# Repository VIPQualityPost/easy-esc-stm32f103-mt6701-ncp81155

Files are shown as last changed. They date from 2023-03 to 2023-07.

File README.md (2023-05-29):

# easy-esc-stm32f103-mt6701-ncp81155

Small, closed loop simpleFOC driver board, that can be assembled for &lt;$10 with mostly basic components at LCSC. has support for current sensing and mounting WS2812 RGBLED for indicating, as well as USB C for serial communication and programming. SWD + UART via STLINK 14 pin connector.

The targe for this project was to create an all-in-one simpleFOC board with high resolution magnetic encoder, current sensing, simpleFOC BLDC driver board which can be assembled with top-side only components, 2 layers, mostly basic components from LCSC library, and which can be powered entirely from USB 2.0 specification (500mA) for mostly use with haptic texture type applications. Additionally, it has a compact size of 38x38mm.

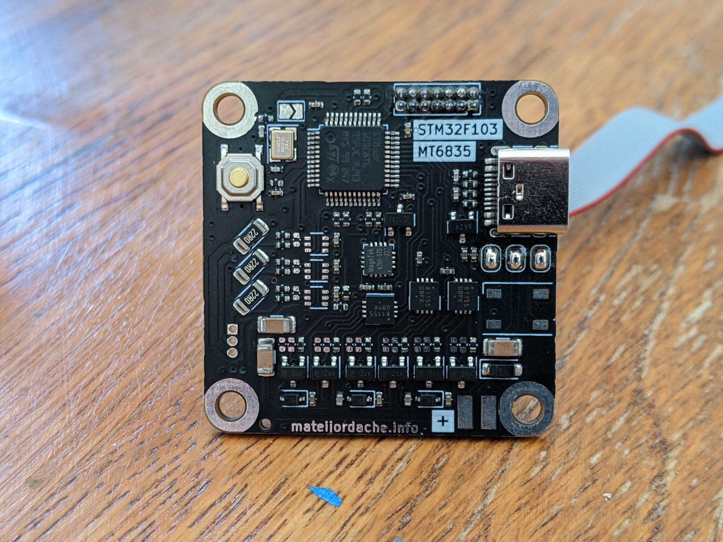
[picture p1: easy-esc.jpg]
3D render of PCB


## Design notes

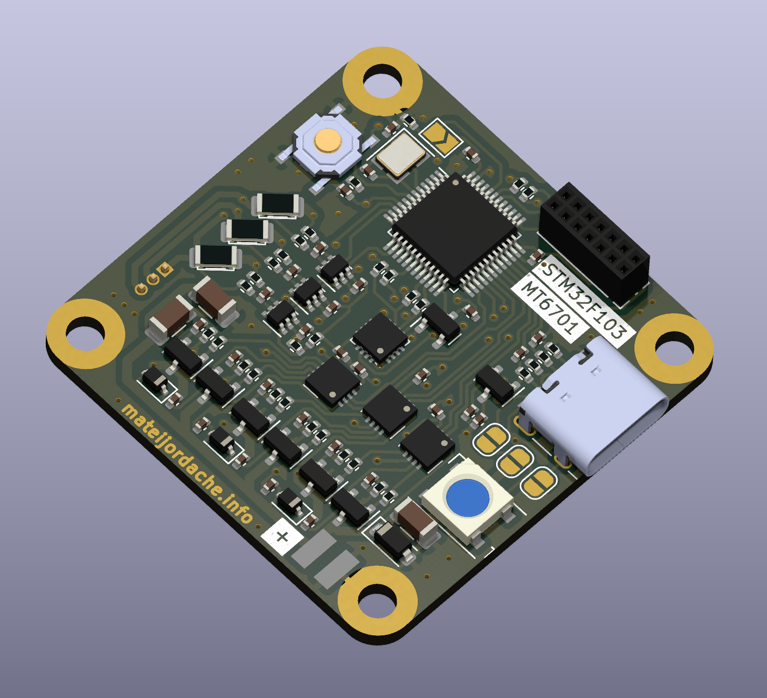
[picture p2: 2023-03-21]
render.png

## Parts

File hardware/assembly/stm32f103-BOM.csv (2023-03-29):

Comment | Designator | Footprint | LCSC
5K | R102,R101 | 0402_R
22R | R106,R107 | 0402_R
1uF | C206,C201,C210,C107,C106 | 0402_C
WS2812 | D101 | SMD_5050
0R | R209,R207,R223,R203,R201,R217,R213,R202,R113,R220,R218,R208,R112,R214,R110,R109 | 0402_R
NCP81155 | U205,U201,U206 | DFN-8_3x3mm | C173765
0.1uF | C101,C212,C218,C211,C109,C111,C110,C108 | 0402_C
1N5819WS | D201,D202,D203 | D_SOD-323 | C191023
22R | R215,R216,R221 | 1206_R
47pF | C105,C104 | 0402_C
10k | R219,R108,R103,R222 | 0402_R
RESET | SW101 | TS-1187A-B-A-B | C318884
LT199 | U204,U203,U202 | SOT-363_SC-70-6 | C2888104
10uF | C214,C215 | 0402_C
AO3400A | Q201,Q205,Q203,Q202,Q101,Q206,Q204 | SOT-23 | C20917
470nF | C222,C205,C223 | 0402_C
5.1k | R105,R104 | 0402_R
20pF | C102,C103 | 0402_C
12MHz | Y101 | Crystal_SMD_3225
HIROSE TYPE C | J101 | HRO_TYPE-C-31-M-12 | C165948
100uF | C221,C220,C213 | 1206_C
STM32F103 | U103 | LQFP-48_7x7mm | C8734
XC6206 | U102 | SOT-23 | C5446
B5819W SL | D204 | D_SOD-123 | C8598
MT6701 | U101 | QFN-16-1EP_3x3mm | C2913974

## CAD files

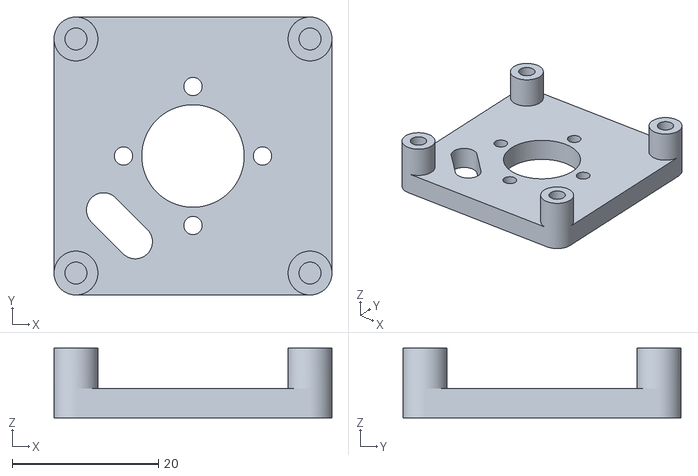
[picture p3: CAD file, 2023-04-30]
mechanical/motormount_b.stl
38.0 x 38.0 x 9.50

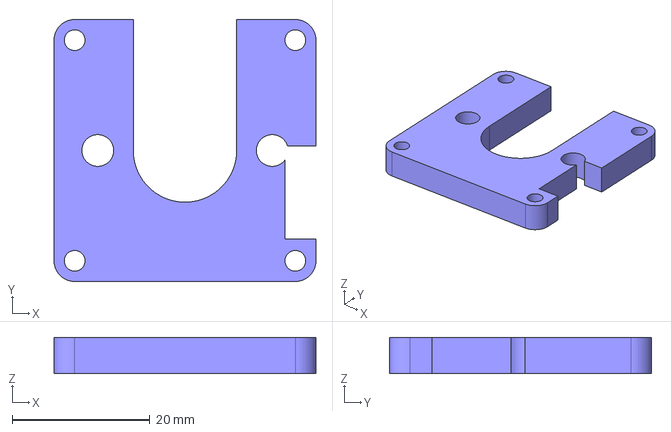
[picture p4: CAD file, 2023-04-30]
mechanical/stm32f103-motormount-back.FCStd
38.0 x 38.0 x 5.25 mm

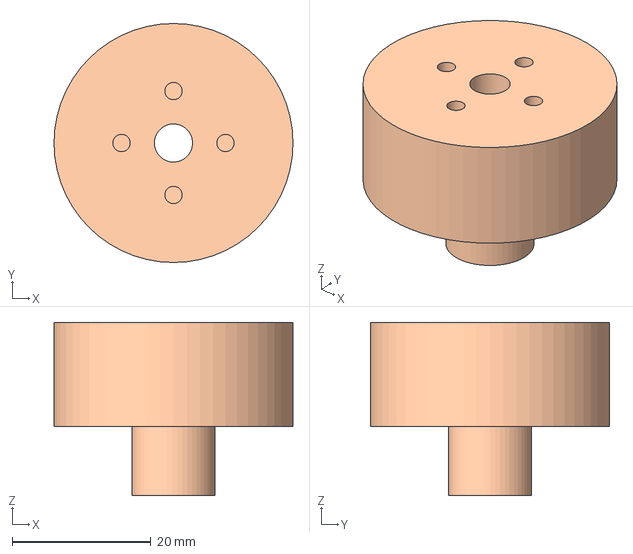
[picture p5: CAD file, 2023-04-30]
mechanical/aliexpress-motor.step
34.5 x 34.5 x 25.0 mm

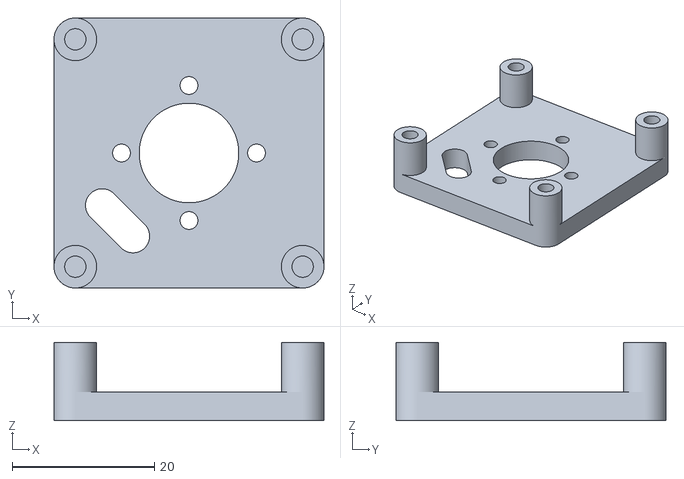
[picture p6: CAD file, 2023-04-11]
mechanical/motormount_test.stl
38.0 x 38.0 x 11.0

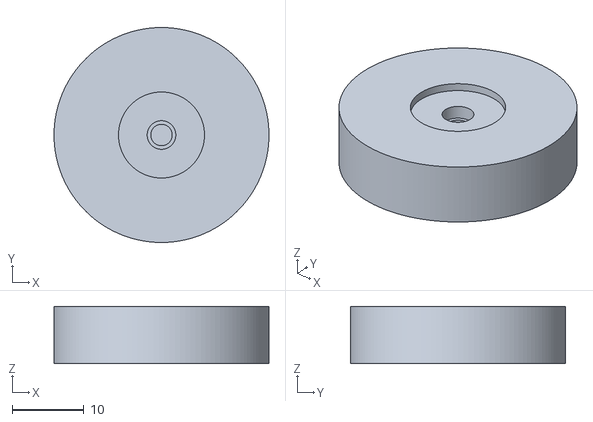
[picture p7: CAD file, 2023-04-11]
mechanical/stm32f103-motormount-back-rotor.stl
30.0 x 30.0 x 8.00

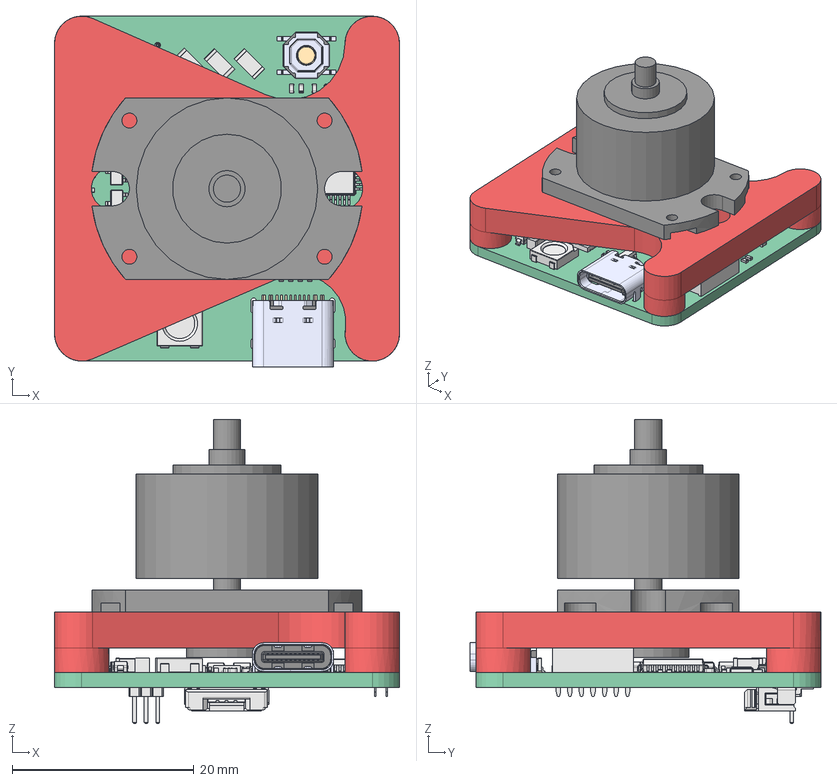
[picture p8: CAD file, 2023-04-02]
mechanical/motormount_front.FCStd
38.0 x 38.6 x 33.5 mm
Pcb_4694
R102_R_0402_1005Metric_309814046252 x 32
C206_C_0402_1005Metric_fbdf68a0e481 x 31
D101_LED_WS2812B_PLCC4_50x50mm_P32mm_7daec3bb67ea
U205_DFN-8-1EP_3x3mm_Pitch0.5mm_7c234c2a8eed x 3
D201_D_SOD_323_6a913e7e0da0 x 3
R215_R_1206_3216Metric_333bfd7ba96b x 3
TS-1187A-B-A-B
TS-1187A-B-A-B001
TS-1187A-B-A-B002
TS-1187A-B-A-B003
TS-1187A-B-A-B004
TS-1187A-B-A-B005
TS-1187A-B-A-B006
U204_SOT_363_SC_70_6_1469dd1663e2 x 3
Q201_SOT_23_4d359ea561da x 8
J102_PinSocket_2x07_P127mm_Vertical_f2266e31e4ba
Y101_Crystal_SMD_3225-4Pin_3.2x2.5mm_af7dcb7e999e
TYPE-C-31-M-12
TYPE-C-31-M-013
TYPE-C-31-M-014
TYPE-C-31-M-015
TYPE-C-31-M-016
TYPE-C-31-M-017
TYPE-C-31-M-018
TYPE-C-31-M-019
TYPE-C-31-M-020
TYPE-C-31-M-021
TYPE-C-31-M-022
TYPE-C-31-M-023
TYPE-C-31-M-024
TYPE-C-31-M-025
TYPE-C-31-M-026
TYPE-C-31-M-027
TYPE-C-31-M-028
TYPE-C-31-M-029
TYPE-C-31-M-030
TYPE-C-31-M-031
TYPE-C-31-M-032
TYPE-C-31-M-033
TYPE-C-31-M-034
TYPE-C-31-M-035
TYPE-C-31-M-036
TYPE-C-31-M-037
TYPE-C-31-M-038
TYPE-C-31-M-039
TYPE-C-31-M-040
TYPE-C-31-M-041
TYPE-C-31-M-042
TYPE-C-31-M-043
TYPE-C-31-M-044
TYPE-C-31-M-045
TYPE-C-31-M-046
TYPE-C-31-M-047
TYPE-C-31-M-048
TYPE-C-31-M-049
TYPE-C-31-M-050
TYPE-C-31-M-051
TYPE-C-31-M-052
TYPE-C-31-M-053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

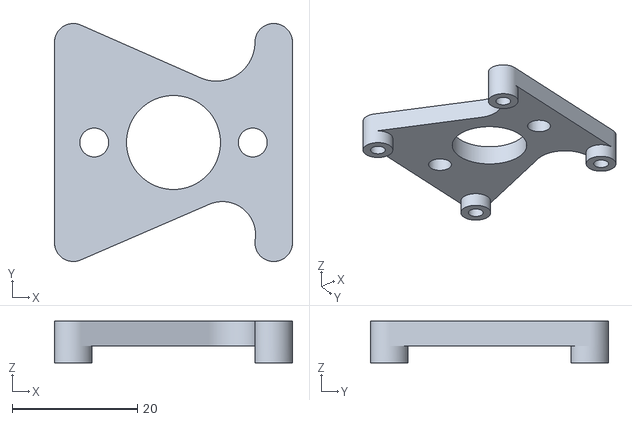
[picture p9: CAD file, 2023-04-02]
mechanical/stm32f103-motormount_top.stl
38.0 x 38.0 x 6.70

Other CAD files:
mechanical/motormount-back-stlinkcutout.stl
mechanical/motormount_back.stl

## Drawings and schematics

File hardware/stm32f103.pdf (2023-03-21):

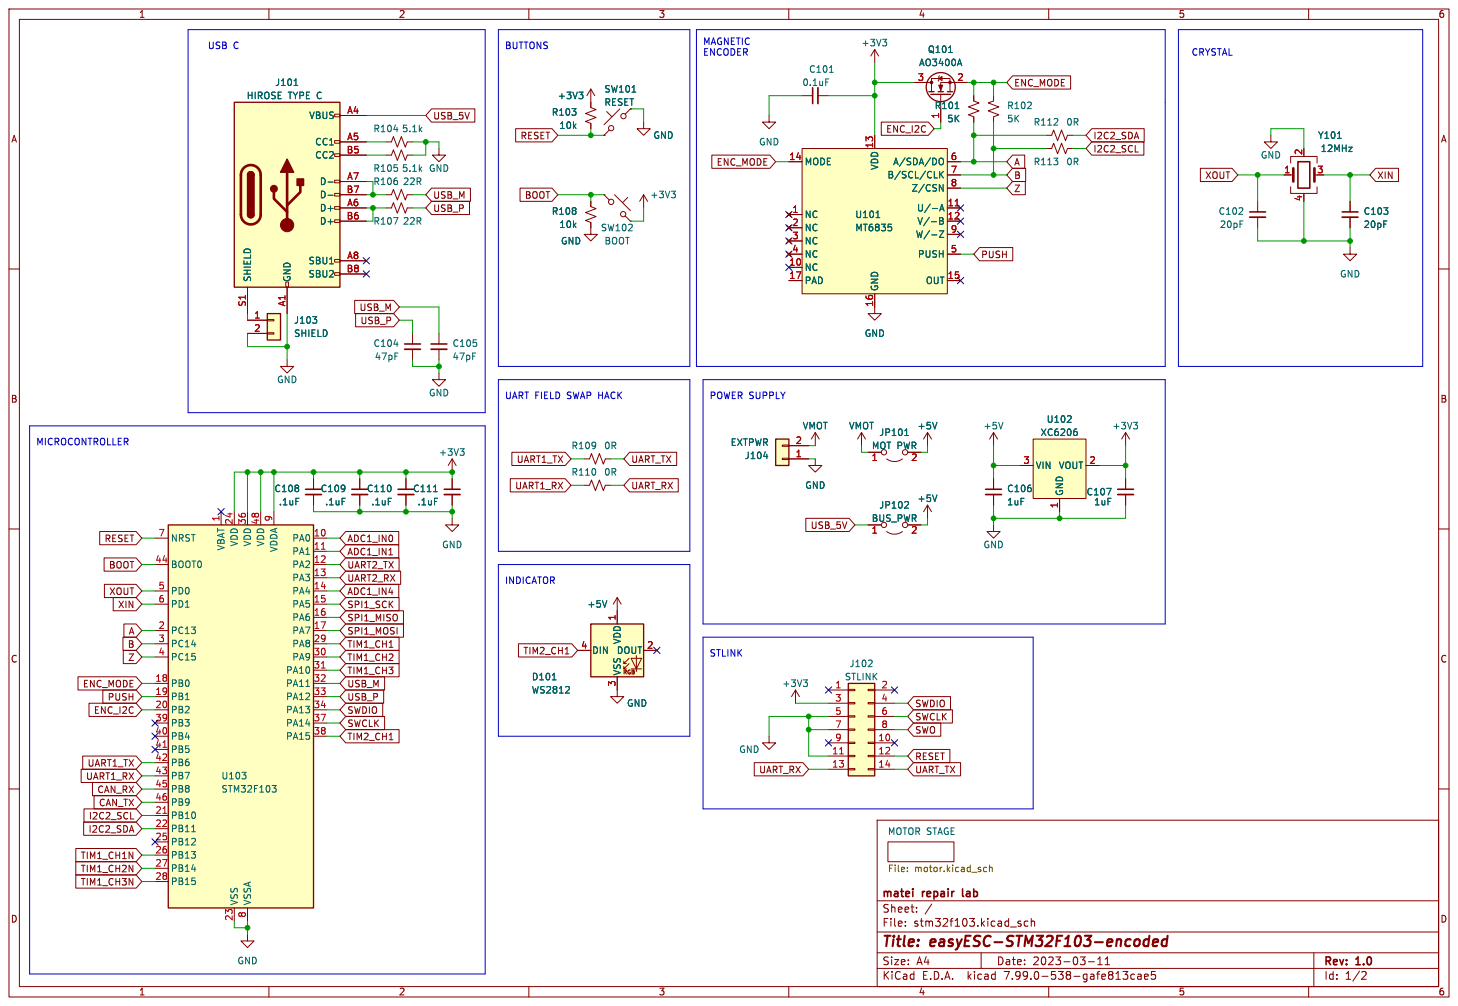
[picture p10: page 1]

UART FIELD SWAP HACK MICROCONTROLLER

1 PA0 10 PA1 11 PA2 12 PA3 13 PA4 14 PA5 15 PA6 16 PA7 17 PB0 18 PB1 19 PC13 2 PB2 20 PB10 21 PB11 22 VSS 23 VDD 24 PB12 25 PB13 26 PB14 27 PB15 28 PA8 29 PC14 3 PA9 30 PA10 31 PA11 32 PA12 33 PA13 34 VDD 36 PA14 37 PA15 38 PB3 39 PC15 4 PB4 40 PB5 41 PB6 42 PB7 43 BOOT0 44 PB8 45 PB9 46 VDD 48 PD0 5 PD1 6 NRST 7 VSSA

File: stm32f103.kicad_sch Sheet: / matei repair lab MOTOR STAGE

Id: 1/2 Title: easyESC-STM32F103-encoded

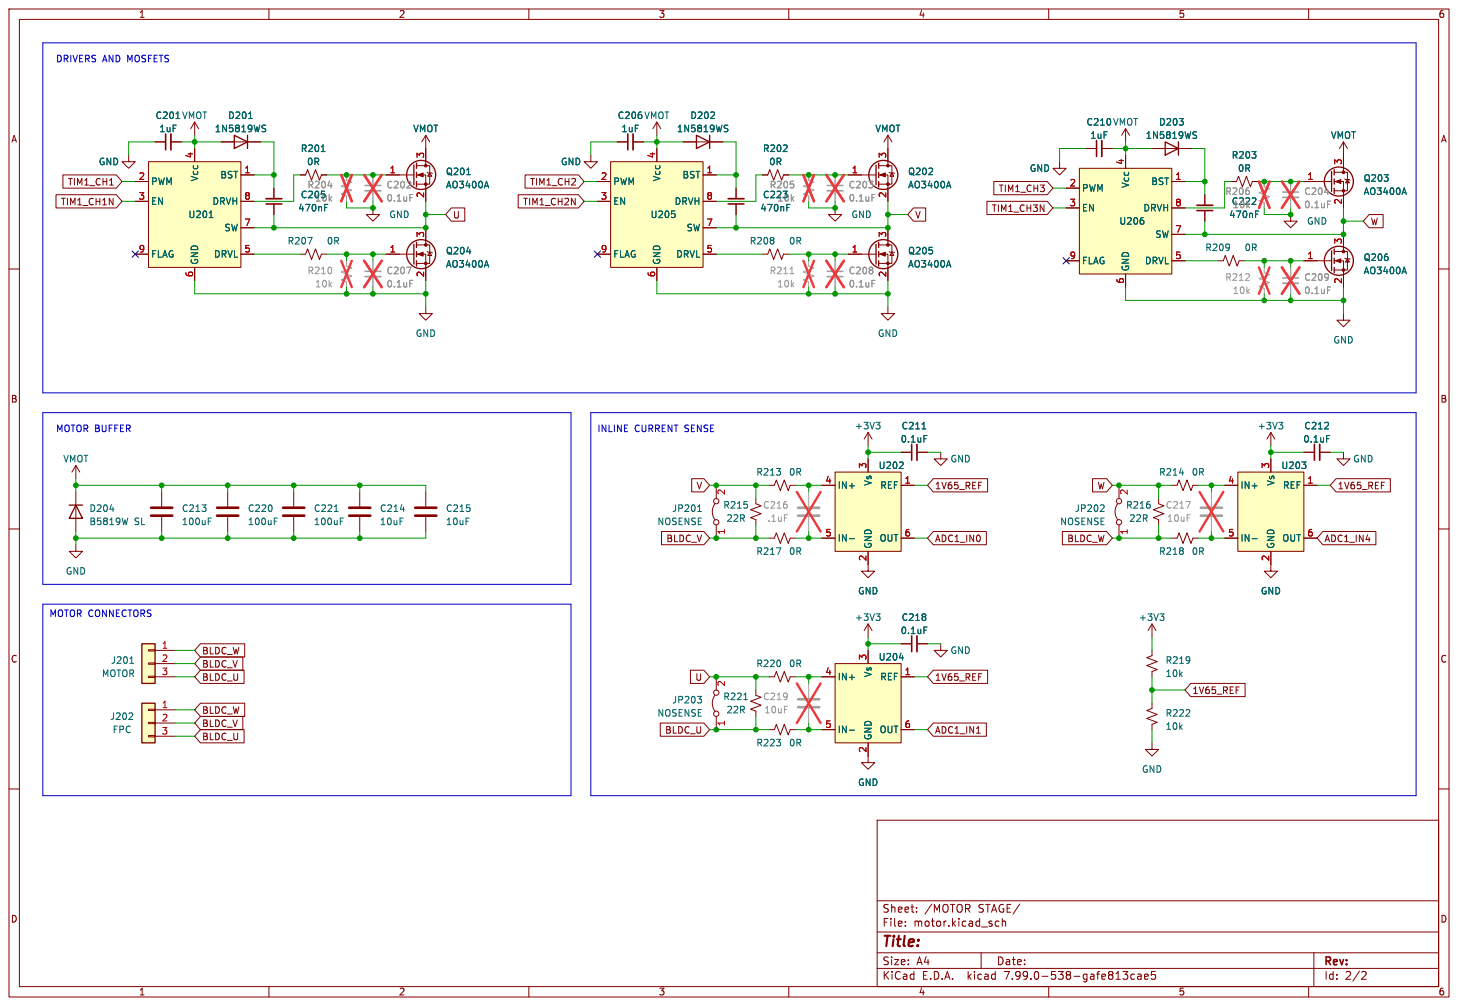
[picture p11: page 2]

6 SW 7 DRVH 8 FLAG 9 U205 VMOT

Id: 2/2 Title: File: motor.kicad_sch Sheet: /MOTOR STAGE/ GND

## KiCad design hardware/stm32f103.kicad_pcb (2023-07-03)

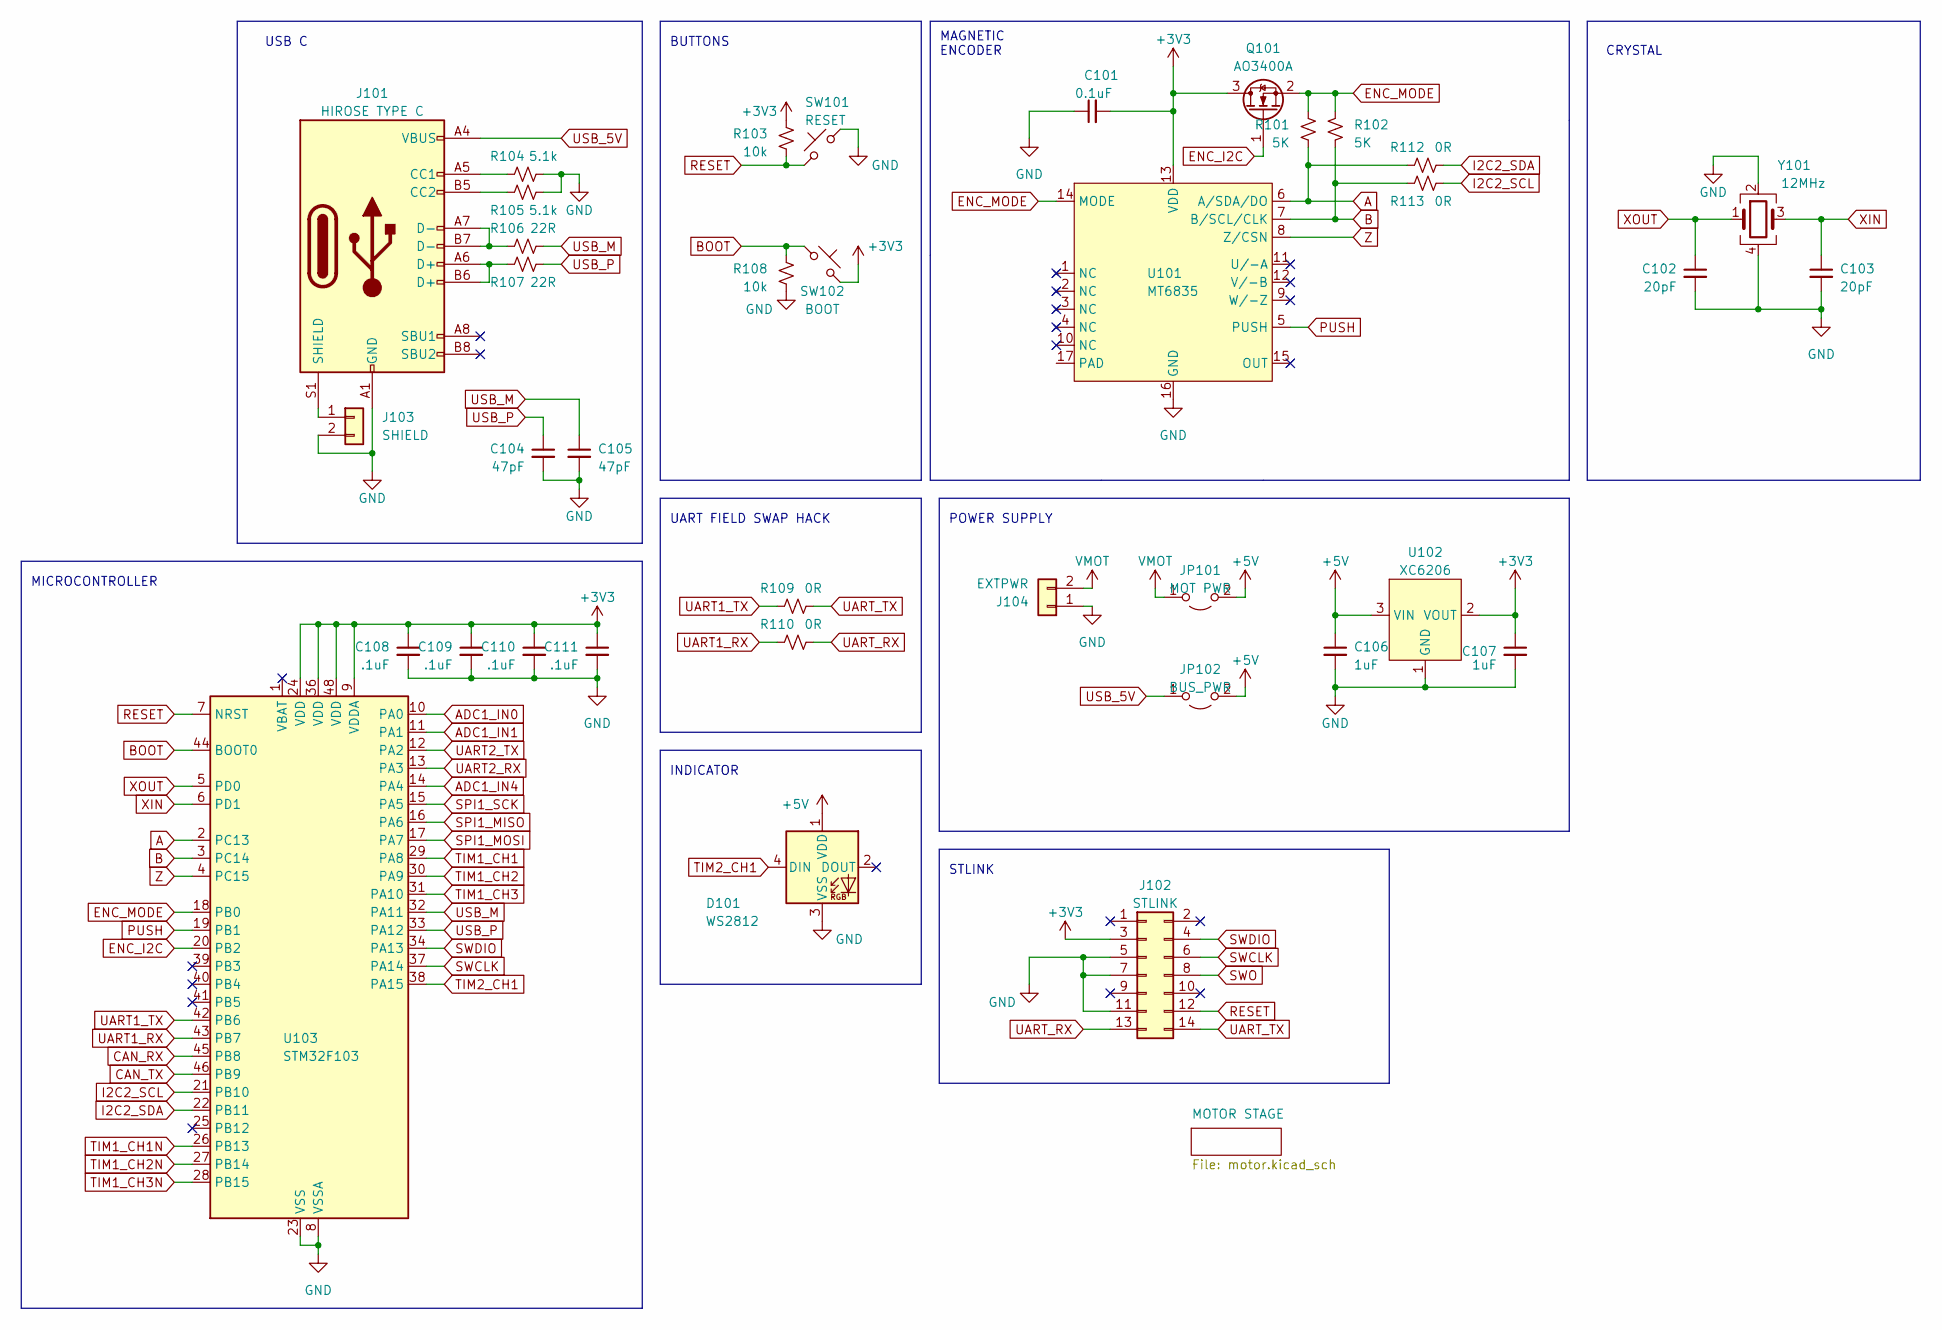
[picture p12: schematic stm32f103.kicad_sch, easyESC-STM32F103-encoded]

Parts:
C101: 0.1uF; C_0402_1005Metric
C102, C103: 20pF; C_0402_1005Metric
C104, C105: 47pF; C_0402_1005Metric
C106, C107: 1uF; C_0402_1005Metric
C108, C109, C110, C111: .1uF; C_0402_1005Metric
D101: WS2812; LED_WS2812B_PLCC4_5.0x5.0mm_P3.2mm
J101: HIROSE TYPE C; USB_C_Receptacle_HRO_TYPE-C-31-M-12
J102: STLINK; PinSocket_2x07_P1.27mm_Vertical
J103: SHIELD; SolderJumper-2_P1.3mm_Open_RoundedPad1.0x1.5mm
J104: EXTPWR; JST-XH-edgemount-2p
JP101: MOT PWR; SolderJumper-2_P1.3mm_Open_RoundedPad1.0x1.5mm
JP102: BUS_PWR; SolderJumper-2_P1.3mm_Open_RoundedPad1.0x1.5mm
Q101: AO3400A; SOT-23
R101, R102: 5K; R_0402_1005Metric
R103, R108: 10k; R_0402_1005Metric
R104, R105: 5.1k; R_0402_1005Metric
R106, R107: 22R; R_0402_1005Metric
R109, R110, R112, R113: 0R; R_0402_1005Metric
SW101: RESET; TS-1187A-B-A-B
SW102: BOOT; SolderJumper-2_P1.3mm_Open_TrianglePad1.0x1.5mm
U101: MT6835; QFN-16-1EP_3x3mm_P0.5mm_EP1.7x1.7mm
U102: XC6206; SOT-23
U103: STM32F103; LQFP-48_7x7mm_P0.5mm
Y101: 12MHz; Crystal_SMD_3225-4Pin_3.2x2.5mm

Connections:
+3V3: C101.2, C107.1, C108.1, C109.1, C110.1, C111.1, J102.3, Q101.3 (D), R103.1, SW102.2, U101.13 (VDD), U102.2 (VOUT), U103.9 (VDDA), U103.24 (VDD), U103.36 (VDD), U103.48 (VDD); also elsewhere on the board
+5V: C106.1, D101.1 (VDD), JP101.2 (B), JP102.2 (B), U102.3 (VIN)
A: R101.2, R112.1, U101.6 (A/SDA/DO), U103.2 (PC13)
ADC1_IN0: U103.10 (PA0); also elsewhere on the board
ADC1_IN1: U103.11 (PA1); also elsewhere on the board
ADC1_IN4: U103.14 (PA4); also elsewhere on the board
B: R102.2, R113.1, U101.7 (B/SCL/CLK), U103.3 (PC14)
BOOT: R108.1, SW102.1, U103.44 (BOOT0)
CAN_RX: U103.45 (PB8)
CAN_TX: U103.46 (PB9)
ENC_I2C: Q101.1 (G), U103.20 (PB2)
ENC_MODE: Q101.2 (S), R101.1, R102.1, U101.14 (MODE), U103.18 (PB0)
GND: C101.1, C102.2, C103.2, C104.2, C105.2, C106.2, C107.2, C108.2, C109.2, C110.2, C111.2, D101.3 (VSS), J101.A1 (GND), J101.A12 (GND), J101.B1 (GND), J101.B12 (GND), J102.5, J102.7, J102.11, J103.2, J104.1, R104.2, R105.2, R108.2, SW101.2, U101.16 (GND), U102.1 (GND), U103.8 (VSSA), U103.23 (VSS), U103.35 (VSS), U103.47 (VSS), Y101.2, Y101.4; also elsewhere on the board
I2C2_SCL: R113.2, U103.21 (PB10)
I2C2_SDA: R112.2, U103.22 (PB11)
unnamed: J101.A5 (CC1), R104.1
unnamed: J101.B5 (CC2), R105.1
unnamed: J101.A6 (D+), J101.B6 (D+), R107.1
unnamed: J101.A7 (D-), J101.B7 (D-), R106.1
unnamed: J101.S1 (SHIELD), J103.1
PUSH: U101.5 (PUSH), U103.19 (PB1)
RESET: J102.12, R103.2, SW101.1, U103.7 (NRST)
SPI1_MISO: U103.16 (PA6)
SPI1_MOSI: U103.17 (PA7)
SPI1_SCK: U103.15 (PA5)
SWCLK: J102.6, U103.37 (PA14)
SWDIO: J102.4, U103.34 (PA13)
SWO: J102.8
TIM1_CH1: U103.29 (PA8); also elsewhere on the board
TIM1_CH1N: U103.26 (PB13); also elsewhere on the board
TIM1_CH2: U103.30 (PA9); also elsewhere on the board
TIM1_CH2N: U103.27 (PB14); also elsewhere on the board
TIM1_CH3: U103.31 (PA10); also elsewhere on the board
TIM1_CH3N: U103.28 (PB15); also elsewhere on the board
TIM2_CH1: D101.4 (DIN), U103.38 (PA15)
UART1_RX: R110.1, U103.43 (PB7)
UART1_TX: R109.1, U103.42 (PB6)
UART2_RX: U103.13 (PA3)
UART2_TX: U103.12 (PA2)
UART_RX: J102.13, R110.2
UART_TX: J102.14, R109.2
USB_5V: J101.A4 (VBUS), J101.A9 (VBUS), J101.B4 (VBUS), J101.B9 (VBUS), JP102.1 (A)
USB_M: C105.1, R106.2, U103.32 (PA11)
USB_P: C104.1, R107.2, U103.33 (PA12)
VMOT: J104.2, JP101.1 (A); also elsewhere on the board
XIN: C103.1, U103.6 (PD1), Y101.3
XOUT: C102.1, U103.5 (PD0), Y101.1
Z: U101.8 (Z/CSN), U103.4 (PC15)

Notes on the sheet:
INDICATOR
USB C
POWER SUPPLY
STLINK
MAGNETIC ENCODER
BUTTONS
UART FIELD SWAP HACK
MICROCONTROLLER
CRYSTAL

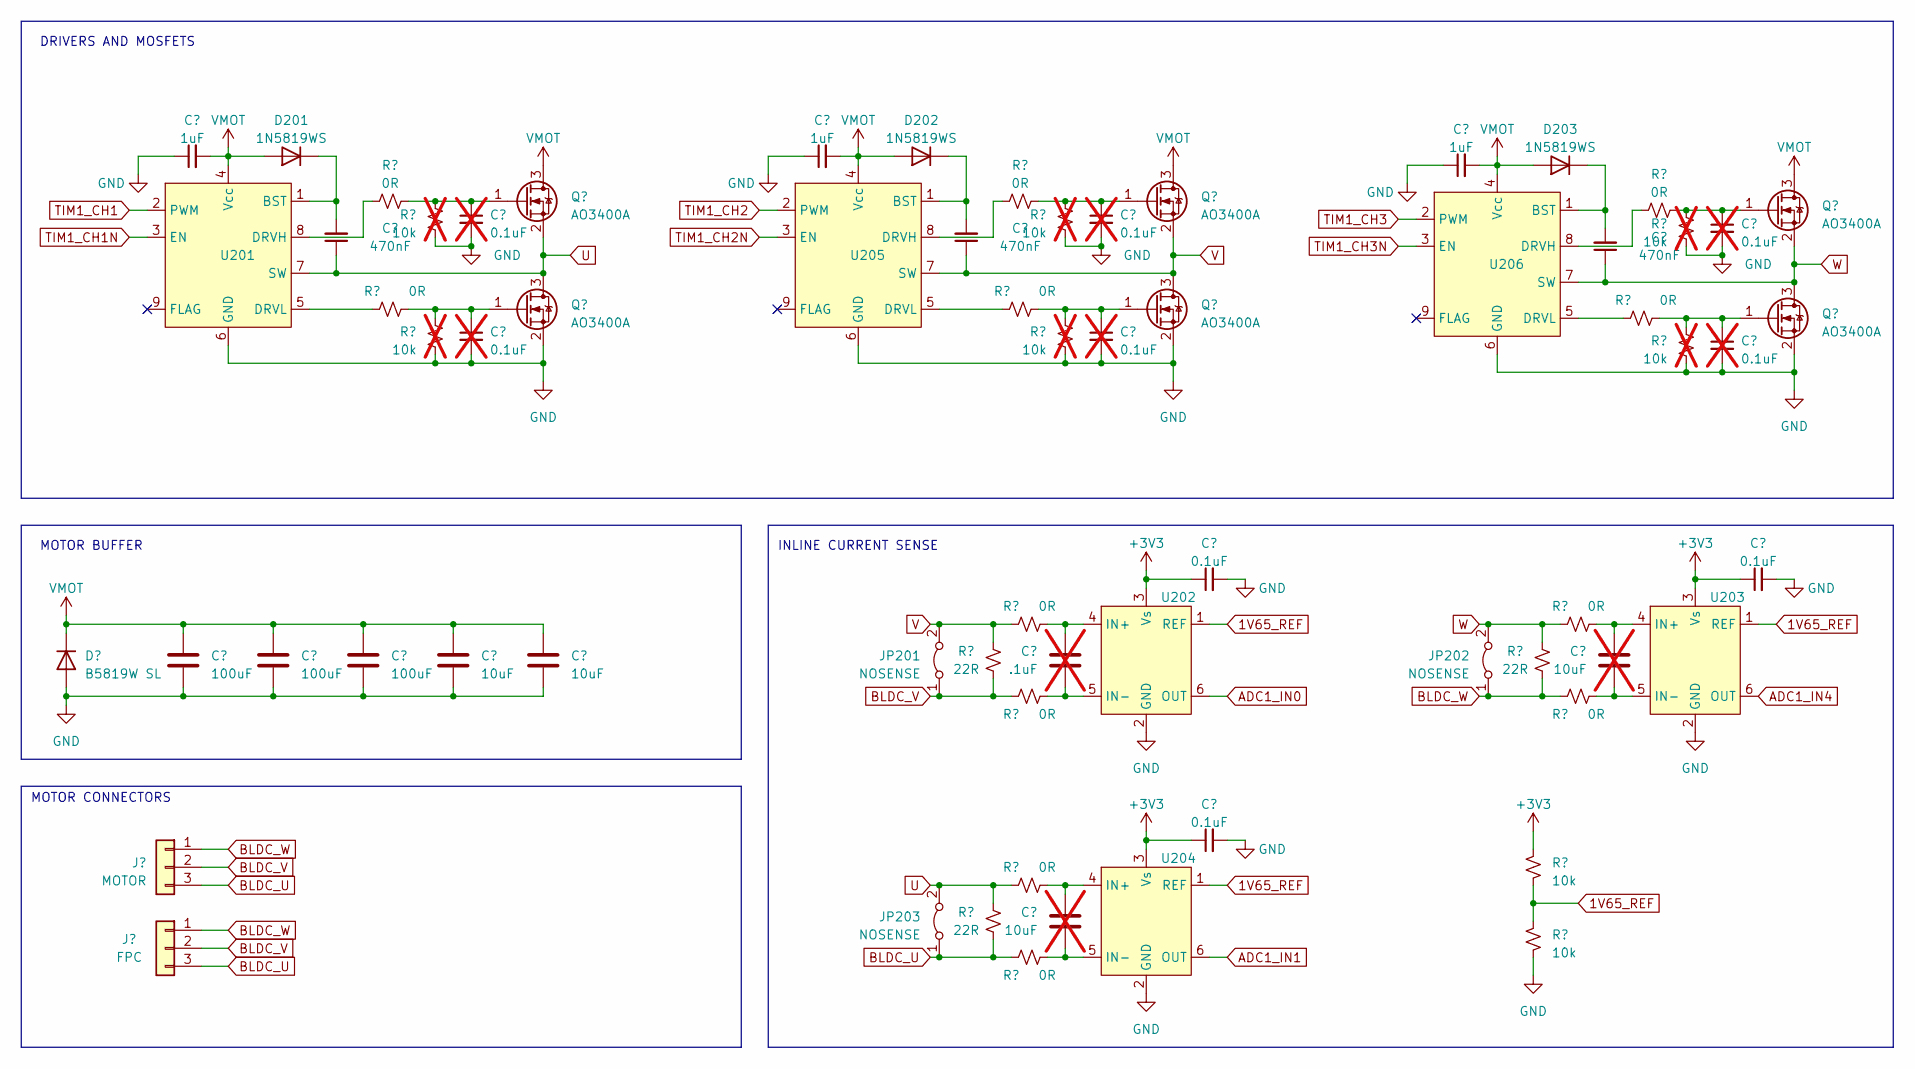
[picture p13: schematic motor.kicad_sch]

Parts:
C201, C206, C210: 1uF; C_0402_1005Metric
C202, C203, C204, C207, C208, C209: 0.1uF; C_0402_1005Metric; not fitted
C205, C222, C223: 470nF; C_0402_1005Metric
C211, C212, C218: 0.1uF; C_0402_1005Metric
C213, C220, C221: 100uF; C_1206_3216Metric
C214, C215: 10uF; C_0402_1005Metric
C216: .1uF; C_0402_1005Metric; not fitted
C217, C219: 10uF; C_0402_1005Metric; not fitted
D201, D202, D203: 1N5819WS; D_SOD-323
D204: B5819W SL; D_SOD-123
J201: MOTOR; PinHeader_1x03_P1.27mm_Vertical
J202: FPC; FPC-SMD_3P-P1.00_HDGC_1.0K-LS-3PWB-BOTTOMCONTACT
JP201, JP202, JP203: NOSENSE; SolderJumper-2_P1.3mm_Open_TrianglePad1.0x1.5mm
Q201, Q202, Q203, Q204, Q205, Q206: AO3400A; SOT-23
R201, R202, R203, R207, R208, R209, R213, R214, R217, R218, R220, R223: 0R; R_0402_1005Metric
R204, R205, R206, R210, R211, R212: 10k; R_0402_1005Metric; not fitted
R215, R216, R221: 22R; R_1206_3216Metric
R219, R222: 10k; R_0402_1005Metric
U201, U205, U206: DFN-8-1EP_3x3mm_P0.5mm_EP1.65x2.38mm
U202, U203, U204: SOT-363_SC-70-6

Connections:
1V65_REF: R219.2, R222.1, U202.1 (REF), U203.1 (REF), U204.1 (REF)
+3V3: C211.1, C212.1, C218.1, R219.1, U202.3 (Vs), U203.3 (Vs), U204.3 (Vs); also elsewhere on the board
ADC1_IN0: U202.6 (OUT); also elsewhere on the board
ADC1_IN1: U204.6 (OUT); also elsewhere on the board
ADC1_IN4: U203.6 (OUT); also elsewhere on the board
BLDC_U: J201.3, J202.3, JP203.1 (A), R221.1, R223.1
BLDC_V: J201.2, J202.2, JP201.1 (A), R215.1, R217.1
BLDC_W: J201.1, J202.1, JP202.1 (A), R216.1, R218.1
GND: C201.1, C202.2, C203.2, C204.2, C206.1, C207.2, C208.2, C209.2, C210.1, C211.2, C212.2, C213.2, C214.2, C215.2, C218.2, C220.2, C221.2, D204.2 (A), Q204.2 (S), Q205.2 (S), Q206.2 (S), R204.2, R205.2, R206.2, R210.2, R211.2, R212.2, R222.2, U201.6 (GND), U202.2 (GND), U203.2 (GND), U204.2 (GND), U205.6 (GND), U206.6 (GND); also elsewhere on the board
unnamed: C205.2, D201.1 (K), U201.1 (BST)
unnamed: C223.2, D202.1 (K), U205.1 (BST)
unnamed: C222.2, D203.1 (K), U206.1 (BST)
unnamed: C202.1, Q201.1 (G), R201.2, R204.1
unnamed: C203.1, Q202.1 (G), R202.2, R205.1
unnamed: C204.1, Q203.1 (G), R203.2, R206.1
unnamed: C207.1, Q204.1 (G), R207.2, R210.1
unnamed: C208.1, Q205.1 (G), R208.2, R211.1
unnamed: C209.1, Q206.1 (G), R209.2, R212.1
unnamed: R201.1, U201.8 (DRVH)
unnamed: R207.1, U201.5 (DRVL)
unnamed: C216.1, R213.2, U202.4 (IN+)
unnamed: C216.2, R217.2, U202.5 (IN-)
unnamed: C217.1, R214.2, U203.4 (IN+)
unnamed: C217.2, R218.2, U203.5 (IN-)
unnamed: C219.1, R220.2, U204.4 (IN+)
unnamed: C219.2, R223.2, U204.5 (IN-)
unnamed: R202.1, U205.8 (DRVH)
unnamed: R208.1, U205.5 (DRVL)
unnamed: R203.1, U206.8 (DRVH)
unnamed: R209.1, U206.5 (DRVL)
TIM1_CH1: U201.2 (PWM); also elsewhere on the board
TIM1_CH1N: U201.3 (EN); also elsewhere on the board
TIM1_CH2: U205.2 (PWM); also elsewhere on the board
TIM1_CH2N: U205.3 (EN); also elsewhere on the board
TIM1_CH3: U206.2 (PWM); also elsewhere on the board
TIM1_CH3N: U206.3 (EN); also elsewhere on the board
U: C205.1, JP203.2 (B), Q201.2 (S), Q204.3 (D), R220.1, R221.2, U201.7 (SW)
V: C223.1, JP201.2 (B), Q202.2 (S), Q205.3 (D), R213.1, R215.2, U205.7 (SW)
VMOT: C201.2, C206.2, C210.2, C213.1, C214.1, C215.1, C220.1, C221.1, D201.2 (A), D202.2 (A), D203.2 (A), D204.1 (K), Q201.3 (D), Q202.3 (D), Q203.3 (D), U201.4 (Vcc), U205.4 (Vcc), U206.4 (Vcc); also elsewhere on the board
W: C222.1, JP202.2 (B), Q203.2 (S), Q206.3 (D), R214.1, R216.2, U206.7 (SW)

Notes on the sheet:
MOTOR BUFFER
MOTOR CONNECTORS
DRIVERS AND MOSFETS
INLINE CURRENT SENSE

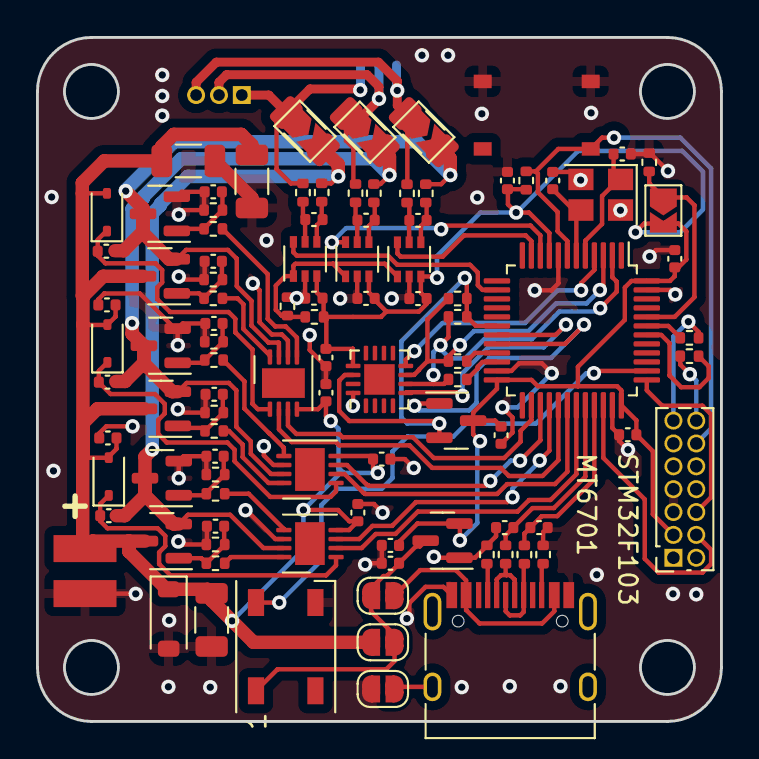
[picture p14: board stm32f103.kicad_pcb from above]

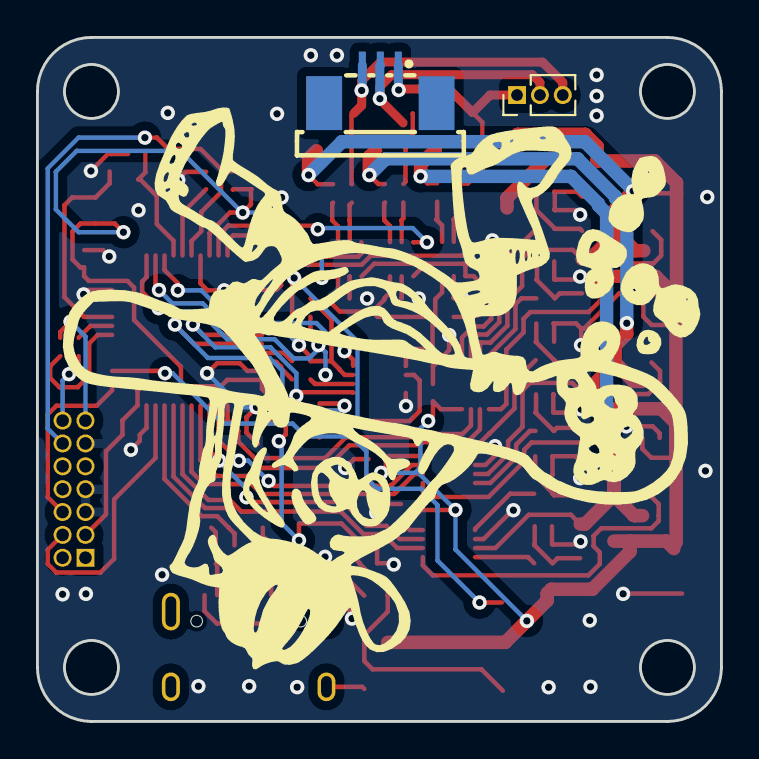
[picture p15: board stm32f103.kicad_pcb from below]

Board: 2 copper layers, 38.0 x 38.0 mm, 104 parts (2 on the bottom side), 68 nets.

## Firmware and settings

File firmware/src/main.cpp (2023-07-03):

#include <Arduino.h>
#include <SimpleFOC.h>
#include "MT6701_I2C.h"
#include "stm32f1xxMT6071_NCP81155.h"

// Motor specific parameters
#define POLEPAIRS 4
#define RPHASE 0.7
#define MOTOR_KV 1000

#ifdef MT6701_I2C
MT6701_I2CConfig_s mt6701_config = {
    .chip_address = 0b0000110,
    .bit_resolution = 14,
    .angle_register = 0x03,
    .data_start_bit = 8};
MT6701_Serial_I2C mt6701 = MT6701_Serial_I2C(mt6701_config);
TwoWire enc_i2c(I2C2_SDA, I2C2_SCL);
#endif

// Prepare SimpleFOC constructors.
BLDCDriver3PWM driver =  BLDCDriver3PWM(PWM_U, PWM_V, PWM_W, EN_U, EN_V, EN_W);
BLDCMotor motor = BLDCMotor(POLEPAIRS,RPHASE,MOTOR_KV);
Commander commander = Commander(Serial);

void doMotor(char *cmd){
  commander.motor(&motor,cmd);
}

void mt6701_i2c_enable(bool state)
{
  digitalWrite(ENC_MODE, state);
  digitalWrite(ENC_I2C_EN, state);
}

void setup(){
  Serial.begin();
  commander.add('M',doMotor,"motor");

  #ifdef SIMPLEFOC_STM32_DEBUG
  SimpleFOCDebug::enable(&Serial);
  #endif

  pinMode(ENC_MODE, OUTPUT);
  pinMode(ENC_I2C_EN, OUTPUT);
  
  #ifdef MT6701_I2C
  // set the MT6701 to Serial mode
  mt6701_i2c_enable(1);
  delay(1000); // let chip settle
  mt6701.init(&enc_i2c);
  motor.linkSensor(&mt6701);
  #endif

  // setup the driver
  driver.pwm_frequency = 25000;
  driver.voltage_power_supply = 5;
  driver.voltage_limit  = 3;
  driver.init();
  motor.linkDriver(&driver);

  // closed loop parameters
  motor.PID_velocity.P = 0.3;
  motor.PID_velocity.I = 20;
  motor.PID_velocity.D = 0.003;
  motor.PID_velocity.output_ramp = 50;
  motor.LPF_velocity.Tf = 0.2;
  motor.LPF_angle.Tf = 0; // try to avoid

  // motor parameters
  motor.voltage_sensor_align = 2;
  motor.current_limit = 0.8;
  motor.velocity_limit = 50;
  motor.controller = MotionControlType::angle;

  motor.init();
  motor.initFOC();

  // Monitor initialization 
  #ifdef HAS_MONITOR
  motor.useMonitoring(Serial);
  motor.monitor_start_char = 'M';
  motor.monitor_end_char = 'M';
  motor.monitor_downsample = 200;
  commander.verbose = VerboseMode::machine_readable;
  #endif

  motor.target = 2;
}

void loop()
{
  motor.loopFOC();
  motor.move();

  commander.run();

  #ifdef HAS_MONITOR
  motor.monitor();
  #endif
}

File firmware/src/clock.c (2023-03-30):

#include <pins_arduino.h>

/**
  * @brief System Clock Configuration
  * @retval None
  */
void SystemClock_Config(void)
{
  RCC_OscInitTypeDef RCC_OscInitStruct = {};
  RCC_ClkInitTypeDef RCC_ClkInitStruct = {};
  RCC_PeriphCLKInitTypeDef PeriphClkInit = {};

  /** Initializes the RCC Oscillators according to the specified parameters
  * in the RCC_OscInitTypeDef structure.
  */
  RCC_OscInitStruct.OscillatorType = RCC_OSCILLATORTYPE_HSE;
  RCC_OscInitStruct.HSEState = RCC_HSE_ON;
  RCC_OscInitStruct.HSEPredivValue = RCC_HSE_PREDIV_DIV1;
  RCC_OscInitStruct.HSIState = RCC_HSI_ON;
  RCC_OscInitStruct.PLL.PLLState = RCC_PLL_ON;
  RCC_OscInitStruct.PLL.PLLSource = RCC_PLLSOURCE_HSE;
  RCC_OscInitStruct.PLL.PLLMUL = RCC_PLL_MUL4;
  if (HAL_RCC_OscConfig(&RCC_OscInitStruct) != HAL_OK)
  {
    Error_Handler();
  }

  /** Initializes the CPU, AHB and APB buses clocks
  */
  RCC_ClkInitStruct.ClockType = RCC_CLOCKTYPE_HCLK|RCC_CLOCKTYPE_SYSCLK
                              |RCC_CLOCKTYPE_PCLK1|RCC_CLOCKTYPE_PCLK2;
  RCC_ClkInitStruct.SYSCLKSource = RCC_SYSCLKSOURCE_PLLCLK;
  RCC_ClkInitStruct.AHBCLKDivider = RCC_SYSCLK_DIV2;
  RCC_ClkInitStruct.APB1CLKDivider = RCC_HCLK_DIV1;
  RCC_ClkInitStruct.APB2CLKDivider = RCC_HCLK_DIV1;

  if (HAL_RCC_ClockConfig(&RCC_ClkInitStruct, FLASH_LATENCY_1) != HAL_OK)
  {
    Error_Handler();
  }
  PeriphClkInit.PeriphClockSelection = RCC_PERIPHCLK_ADC|RCC_PERIPHCLK_USB;
  PeriphClkInit.AdcClockSelection = RCC_ADCPCLK2_DIV2;
  PeriphClkInit.UsbClockSelection = RCC_USBCLKSOURCE_PLL;
  if (HAL_RCCEx_PeriphCLKConfig(&PeriphClkInit) != HAL_OK)
  {
    Error_Handler();
  }
}

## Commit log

2023-03-21 add schematic pdf
    [motor.kicad_sch, stm32f103.kicad_sch]
2023-03-29 add in platformio configuration
    [motor.kicad_sch, stm32f103-BOM.csv, stm32f103.kicad_sch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]
2023-04-02 get closed loop working, fix i2c driver for mt6701
    [motormount_back.stl, motormount_front.FCStd, stm32f103-motormount-back.FCStd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]
2023-04-11 Auto-commit Tue Apr 11 10:47:16 EDT 2023
    [motormount_test.stl, stm32f103-motormount-back-rotor.stl, stm32f103-motormount-back.FCStd]
2023-04-30 Auto-commit Sun Apr 30 10:54:41 EDT 2023
    [aliexpress-motor.step, motormount-back-stlinkcutout.stl, motormount_b.stl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]
2023-06-25 Revert to working firmware, clean up gitignore, remove unused library from platformio.ini
    [main.cpp]
2023-06-25 tune PID params
2023-06-27 fix PID gains
2023-07-02 setup serial device settings on session
2023-07-03 Remove kicad_pcb from gitgnore
    [stm32f103.kicad_pcb]
2023-07-03 Fix build issues from updated STSTM32 platform
    [main.cpp]
